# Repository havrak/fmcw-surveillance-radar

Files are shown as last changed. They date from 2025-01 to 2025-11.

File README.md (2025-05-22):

# FMCW Surveillance Radar

This is repo for my bachelors thesis.
This thesis presents the development of a surveillance radar system utilizing the SiRad Easy FMCW module.
FMCW (Frequency-Modulated Continuous Wave) technology enables precise distance measurement of targets while maintaining low power consumption.
Initially, the module’s capabilities are analyzed to identify its operational limits.
A custom two-axis rotary platform is then designed and constructed to enable mechanical beam steering, achieving three-dimensional spatial scanning.
The platform is controlled by an ESP32C6 microcontroller, implementing a G-code-like command interface for convenient operation.
MATLAB is employed to integrate the radar module with the platform to process the acquired data.
While the system’s performance limitations preclude real-time tracking of moving targets, it demonstrates functionality in monitoring diverse static environments, ranging from high-resolution close-range applications to long-range detection of targets up to 300 meters.
To accommodate these use cases, the processing pipeline is designed for flexibility, enabled by great degree of configurability.

#### Two-Axis Platform

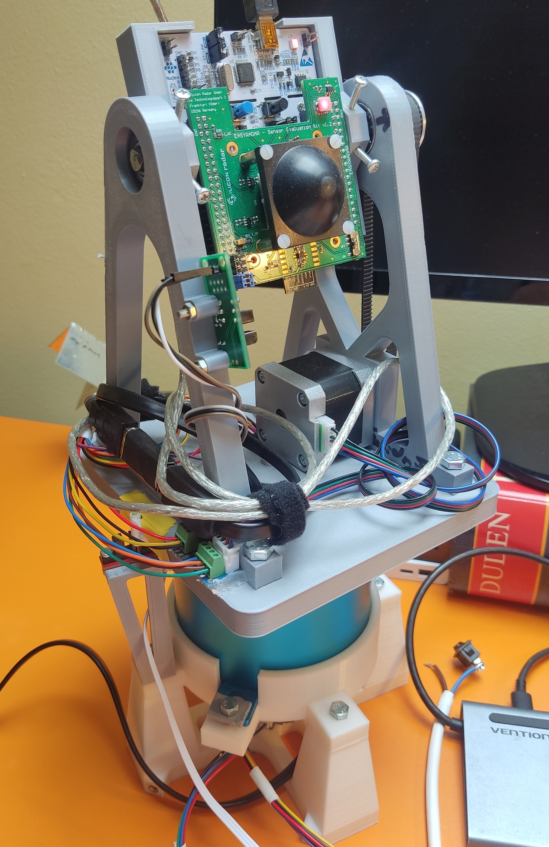
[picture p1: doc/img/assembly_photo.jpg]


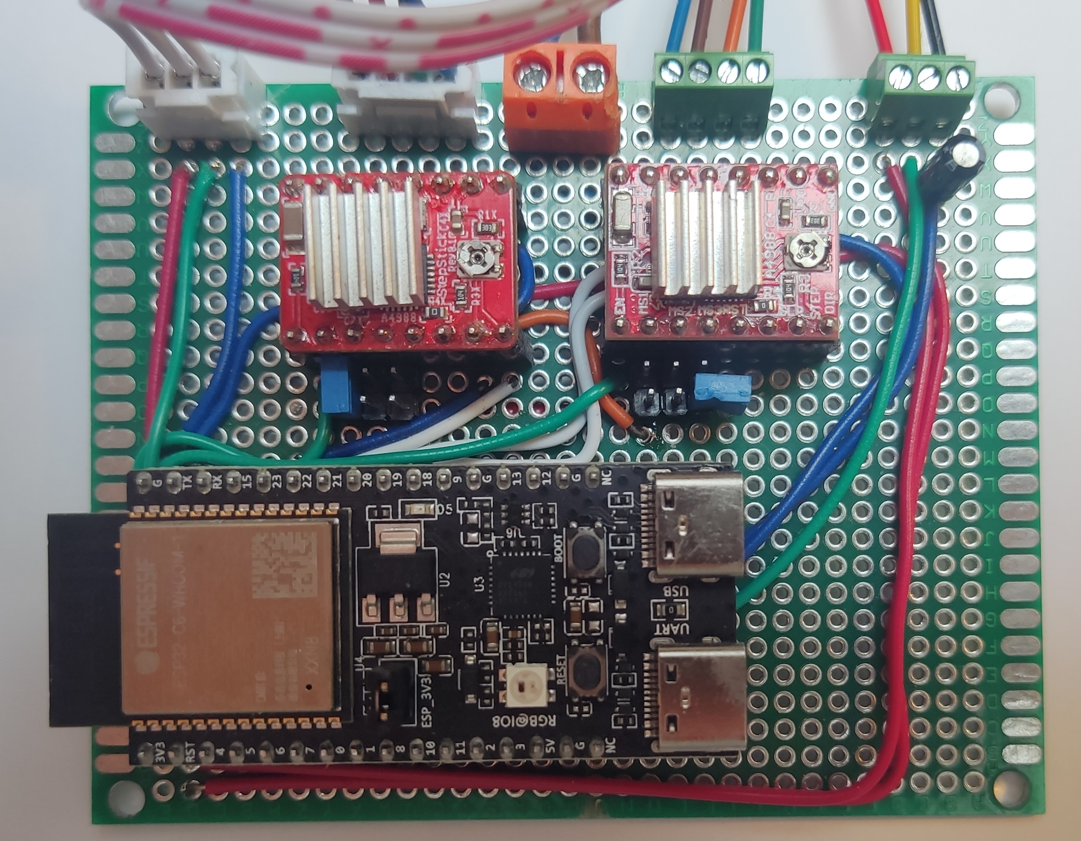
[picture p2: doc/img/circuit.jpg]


#### MATLAB application

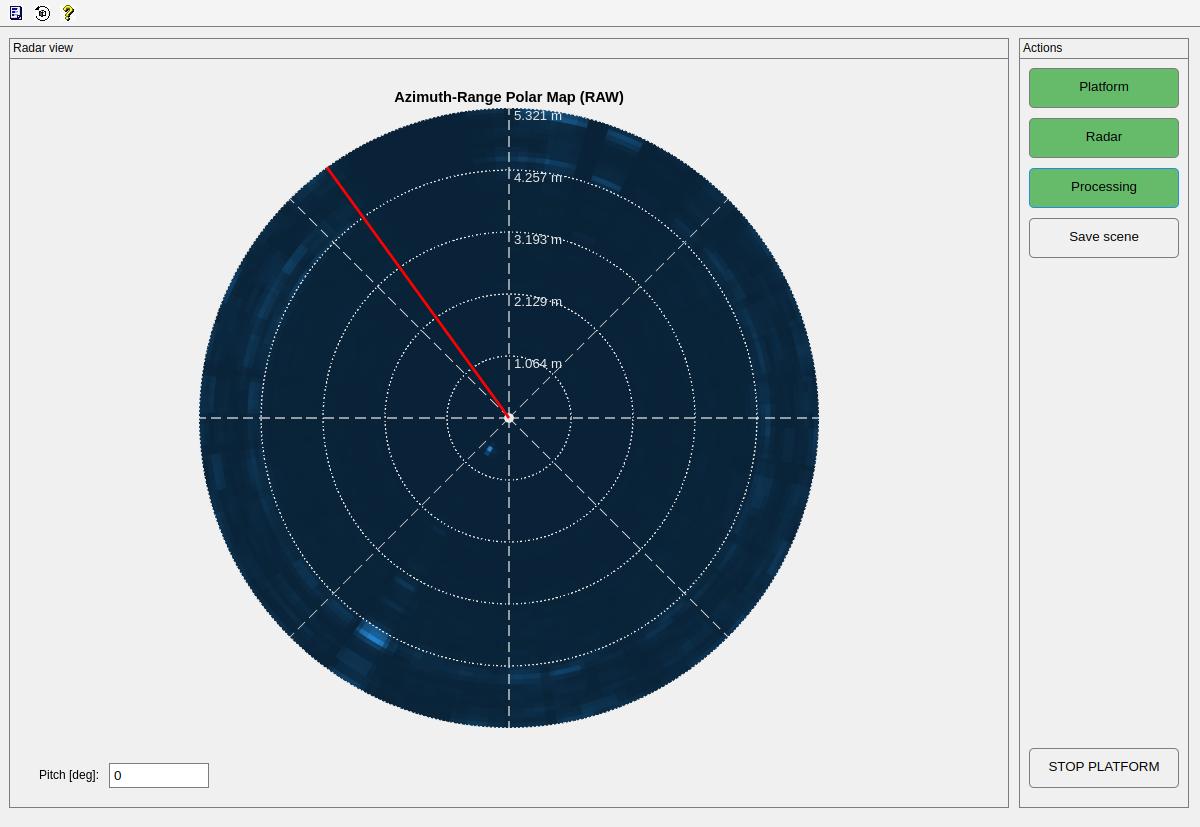
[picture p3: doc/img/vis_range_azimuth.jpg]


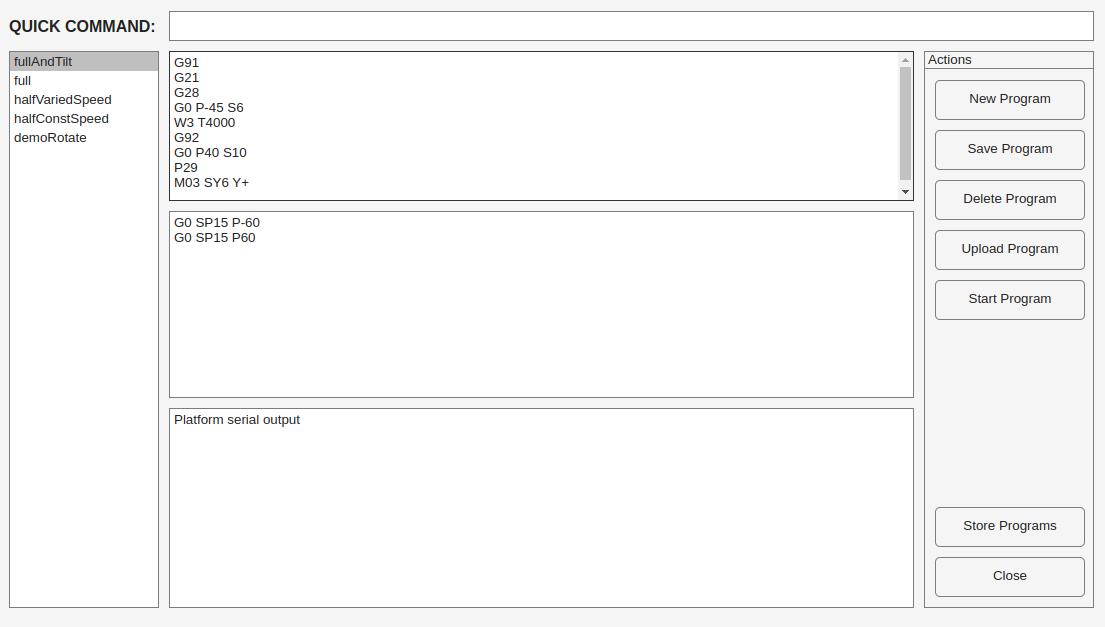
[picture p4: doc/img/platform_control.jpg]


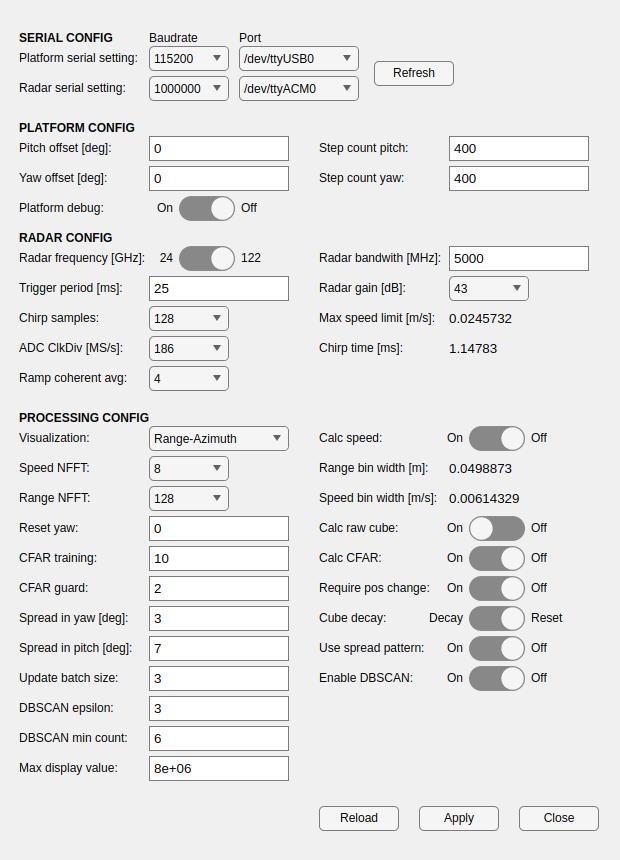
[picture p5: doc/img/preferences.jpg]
preferences


## Folder structure
* notes
	* personal notes on workings of Surveillance radars, ideas for processing and such
	* aren't part of any official publication of this thesis
* doc - full official documentation
* matlab - contains all MATLAB code that is responsible for processing data from the radar, displaying it and interfacing with indexing table
* indexing-table - contains all things related to custom two axis indexing table created for this project
	* esp32 - code for ESP32 microcontroller powering the indexing table
	* cad - cad files of mechanical parts and custom PCBs

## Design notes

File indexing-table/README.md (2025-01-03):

# Indexing table directory

This directory contains all resources regarding custom 2 axis rotary indexing table that has been constructed for this application.
Directory `esp32` concerns firmware for esp32 microcontroller driving the platform.
Cad directory than necessary cad files to 3D print additional components.

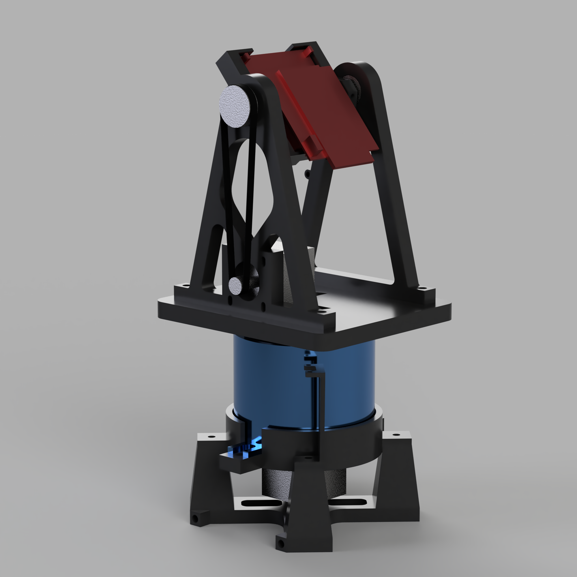
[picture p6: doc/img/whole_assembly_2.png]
render




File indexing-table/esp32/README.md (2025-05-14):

# ESP32 firmware to control indexing table
As of now code relies on proprietary libraries that are not included in this repository. After the project is closed to being finished, these libraries will be stripped to their bare minimum and included in this repository.

Following codebase is written entirely for esp-idf framework. While hal layer used is mimicking arduino, there are differences and thus simple porting of the code to arduino is not possible.
Configuration of the device is done primarily with Kconfig under esp-idf. While runtime configuration with storing to flash is possible, it is not needed for the current application and would result in unnecessary slowdowns.

# Constants
* these parameters are defined in Kconfig and will require recompilation of the firmware to change
* STEPPER_Y_STEP_COUNT, STEPPER_P_STEP_COUNT - number of steps in a single rotation on horizontal and pitch
	* can be changed on the fly with M92 command, however changes are not persistent
* STEPPER_Y_PIN_DIR, STEPPER_Y_PIN_STEP, STEPPER_P_PIN_DIR, STEPPER_P_PIN_STEP - pins used for direction and step signals
* STEPPER_Y_PIN_ENDSTOP, STEPPER_P_PIN_ENDSTOP - pins used for endstop signals
* STEPPER_MAX_SPEED - maximum speed in rpm
* STEPPER_DEFAULT_SPEED - default speed in rpm
* STEPPER_MIN_SPINDLE_TIME - minimum time in ms between two steps in spindle Mode
	* needed to maintain valid information about current position
	* never set bellow ~30 ms
* STEPPER_HAL_TIMER_PERIOD  - timer period (number of ticks per 1 period)
* STEPPER_HAL_TIMER_RESOLUTION - timer resolution (frequency of the timer)
	* these two influence how quickly will the 16 bit timer fill up, for higher RMP period must be lower, for lower RPM period must be higher

# Features
* two different units: degrees and steps
* two different positioning modes: absolute and relative
* common commands like simple movement, homing, setting speed and such, turning on/off are supported
* non standard GCode commands
	* imposing limits on movement - allowed positions of the steppers can be restricted
	* spindle mode - steppers can freely transitions between acting as steppers and as spindles (continuos motion)
	* programming - user can program in sequence of movements that can be executed with one command
		* these can be looped indefinitely or use simple one layer deep for loop
	* maintaining synchronization between two steppers
		* if both steppers are moving, next command is executed only after both steppers reach their target

## Behavior of limits
* user can impose limits on movement of both steppers this can be done via M201 command
* if user wishes to disable limits, they can do so with M202 Command
* movement must be restricted from two sides, restricting only one side doesn't make any sense as we are spinning in a circle
* limits are within single rotation of stepper, it is impossible to allow limited number of full rotations
* there are two possible basic setting for angles
	* low < high - we are restricted to range [low, high]
	* low > high - we are restricted to range [low, 360] U [0, high]

### Absolute positioning
* all angles are automatically normalized to [0, 360] range, or [0, STEP_COUNT] if we are in steps mode
* no limits
	* stepper will take shortest path to the target
* range: [low, high]
	* if target is outside of the range, it will be adjusted to the closest limit
	* than movement is rather straightforward as we can move only in one direction
* range: [low, 360] U [0, high]
	* if target is outside of the range, it will be adjusted to the closest limit
	* we firstly calculate average of the two limits than:
		* anything in [0, avg] is adjusted to high
		* anything in [avg, 360] is adjusted to low
	* again only one direction of movement is possible

### Relative postioning
* number of steps in single command is limited to +-32767, this is hardware/esp-idf private API limitation and cannot be changed
* no limits
	* stepper will do as many steps as are requested (limited to +-32767)
* range: [low, high]
	* if target is outside of the range, it will be adjusted to the closest limit
* range: [low, 360] U [0, high]
	* if target is outside of the range, it will be adjusted to the closest limit
	* if we are decrementing the angle we can only go to high limit
	* if we are incrementing the angle we can only go to low limit

# Communication

WARNING: DO NOT use this device without first reading the documentation. Commands might have similar names and structures as in common G-code but their behavior can be radically different as this device has rather specific requirements.

## Motor control
* axis descriptors: Y for yaw (horizontal) and P for pitch (tilt)
* M80: turn on high voltage power supply
* M81: turn off high voltage power supply
* M82: stop steppers and clear queues
* G20: set units to degrees
* G21: set units to steps
* G90: absolute positioning
	* Y - set absolute positioning on yaw
	* P - set absolute positioning on pitch
	* NOTE: absolute positioning is not available in spindle mode, if you issue a M03 command to stepper in absolute positioning mode, it will be automatically switched to relative positioning and throw an error
	* if no argument is provided both axis are switched to relative positioning
* G91: sets relative positioning
	* Y - set relative positioning on yaw
	* P - set relative positioning on pitch
	* if no argument is provided both axis are switched to relative positioning
* G92: set current position as 0
	* Y - set current position as 0 on yaw
	* P - set current position as 0 on pitch
	* if no argument is provided both axis are set to 0
	* NOTE: executes only when no other commands are queued in stepper queues
* G28: auto home
	* Y - home yaw
	* P - home pitch
	* if no argument is provided both axis are are homed
* stepper mode
	* only active if spindle mode is off
	* G0: move to/by given angle/steps
		* S<SPEED> - fallback speed
		* SY<SPEED> - speed for yaw motor
		* Y - angle by/to rotate in yaw
		* SP<SPEED> - speed for pitch motor
		* P - angle by/to rotate in pitch
		* speed needs to be provided, if number of steps is set but speed is not ERR 2 is returned
* spindle mode
	* beware when using spindle in programming mode one can desynchronized two command queues, this "issue" will be fixed and is up to user to handle as there is no clear way to decipher user intentions in programm in order to prevent it
	* M03:  Start spindle mode
		* S<SPEED> - fallback speed
		* SY<SPEED> - speed for yaw motor
		* Y<+/-> - start spin with yaw motor clockwise/anticlockwise
		* SP<SPEED> - speed for pitch motor
		* P<+/-> - start spin pitch motor clockwise/anticlockwise
		* NOTE: spindle will always spin at least for STEPPER_MIN_SPINDLE_TIME ms, thus theoretically to spin for N seconds would would have to substract STEPPER_MIN_SPINDLE_TIME from the time you want to spin, however timing here is quite finicky so correction probably will not secure exact number of steps
	* M05:  Stop spindle spinning.
		* Y - stop spindle regime on yaw
		* P - stop spindle regime on pitch
		* NOTE: spindle mode will also automatically end if stepper receives G0 command or if another M03 command is issued
		* if no argument is present neither axis will be stopped
* M92: set step count on steppers
	* Y<STEPS: set step count on Yaw
	* P<STEPS>: set step count on Pitch
	* default step count is defined in Kconfig
* M201: set limits on steppers
	* LY<ANGLE>: low limit on yaw
	* HY<ANGLE>: high limit on horizontal Stepper
	* LP<ANGLE>: low limit on pitch
	* HP<ANGLE>: high limit on pitch
	* ANGLE is given in degrees if unit is set to degrees (0-360), otherwise in steps (0-STEP_COUNT)
	* either no limits are placed on axis or both limits are placed, if user tries to impose just one limit whole axis will not be processed
	* NOTE: keep in mind that if limits are imposed and current postion is not within them, you will have to get the device within limits in one G0 command
* M202: disable limits
	* Y - disable limits on yaw
	* L - disable limits on pitch

### Programming movements
* device allows to preprogram sequence of movements that can be executed with one command, or looped continuously
* programms are not stored in flash, but in ram for now. Permanent storage of movements is done in MATLAB's programm configuration file
* if programm requires movement on both axis it is executed in parallel and next command is executed only after both axis reach their target
* program structures
	* header declaration
		* executed only once
		* used to set initial position, units, positioning mode, or home the device
	* main body
		* used for actual movement
		* if command P29 is issued it will be executed in a loop indefinitely loop
		* can be left empty
* P0 - stop executing programm (only one programm can be active at one time)
* P1 <command_id> - run command with given id
* P2 <command_id - delete command with given id
* P90 <command_id> - start programming mode with given id
	* if programm already exists it will be overwritten, changing programs post creation is not possible
	* upon entering programming mode all commands are stashed and not executed
	* programming begins with header declaration
		* commands declared in header are executed before any other commands
		* if programm is looped, header will be executed only once
		* can be used to set initial position, units, positioning mode, or home the device
* P91: called within programming context, advances programming from header declaration to main body
* P92: ends programming of the main body
	* NOTE: if loops are not closed, programm will not be saved and P92 command is disregarded
* P21: for loop declaration
	* I<ITERATIONS> - number of iterations for loop will take
* P22: end of loop
	* if iterations are not exhausted, programm will jump back to P21 (respectively command right after it)
* P29: declares looped programm, these programs will loop indefinitely until stopped
	* NOTE: only applicable in header declaration
* W0: wait command (seconds)
	* Y<TIME> - wait on yaw
	* P<TIME> - wait on pitch
* W1: wait command (milliseconds)
	* Y<TIME> - wait on yaw
	* P<TIME> - wait on pitch

#### Example of programming

| Command | Mode | Description |
|---|---|---|
| P90 prog | General -> Header dec  | start programming mode with programm id of 1 |
| G91 | Header dec | set relative positioning |
| G20 | Header dec | set units to degrees |
| G92 | Header dec | set current position as home |
| P29 | Header dec | declare looped programm |
| M03 SY6 Y+ | Header dec -> Main dec | set yaw to be in spindle mode |
| P91 | Main dec | start declaration of main loop |
| G0 SP30 P100  | Main dec | move pitch by 100 degrees at 30 rpm |
| G0 SP30 P-100 | Main dec | move pitch by -100 degrees at 30 rpm |
| P92 | Main dec | end programming |

### Special advanced commands
* WARN: usage of these commands is not recommended and can lead to unexpected behavior
* their primary usecase is to enable real time control over the device - for example to do tracking of some object
* M82: stop steppers and clear queues
	* similar to M80, however stop command is issued to the steppers instead of shutting them down
	* this means steppers will finish their current movement and then stop - thus data about current position should be still valid
	* used in conjunction with G3 to setup environment for real time control
* G3: direct control over steppers
	* G3 command skip whole scheduling routine and put command directly into stepper queues
	* NOTE: limits are not and cannot be checked
	* NOTE: all values are interpreted as steps
	* NOTE: if M82 is issued beforehand than G3 command should not lead to invalidation of current position
	* S<SPEED> - fallback speed
	* SY<SPEED> - speed for yaw
	* Y - angle by/to rotate in yaw
	* SP<SPEED> - speed for pitch
	* P - angle by/to rotate in pitch
* W3: wait in application layer
	* T<TIME> - time to wait for in ms
	* pauses execution in application layer

# Uplink from the device
* !P <TIMESTAMP>, <HORIZONTAL_ANGLE>, <TILT_ANGLE>
	* roughly every 20 ms device sends its current postion up with serial line
* !R OK or !R ERR <CODE>
	* upon receiving command from the host, device will send back an acknowledgement
	* in case of an error reported please consult following table

| Error code | Description |
|---|---|
| 1 | command wasn't able to be decoded |
| 2 | command code is valid but it's arguments aren't |
| 3 | command was processed, should be added to noProgrammQueue but we failed to get a lock |
| 4 | command exists but isn't yet supported by the hardware |
| 5 | we are either running homing or some programm thus new incoming commands will not be process |
| 6 | command might be fine but code runned into unexpected occurrence |
| 7 | indicated that program has unclosed for loop, it is recommended to delete whole program and start again |
| 8 | command is not valid in current context |

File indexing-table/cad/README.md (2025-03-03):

# CAD files for the indexing table

This directory contains CAD files for the indexing table. Models are exported as Fusion Archives.

* **static base v2** - main base on which entire structure rests
* **slipring mounting bracket** - mounting bracket that fixes slipring to static base
* **horizontal endstop holder** - attaches to slipring mounting bracket and provides mounting points for horizontal endstop
* **rotary base 1** - mount on top of slipring and provides points to attach rest of superstructure
* **SiDAR mount** - bracket to hold SiDAR devkit and enable tilt
* **superstructure left** - attaches to rotary base, holds radar and provides mounting point for tilt endstop
* **superstructure right** - attaches to rotary base, holds radar and tilt stepper motor

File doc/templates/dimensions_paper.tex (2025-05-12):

%%% Different page dimensions used on thesis
\def\PageLayoutSingle{single}
\def\PageLayoutSingleNoPrint{single-no-print}
\def\PageLayoutDouble{double}
\def\PageLayoutDoubleNoPrint{double-no-print}

%% Single page print
\ifx\PageLayout\PageLayoutSingle
\documentclass[a4paper,oneside,12pt]{report}
\setlength\textwidth{145mm}
\setlength\textheight{251mm}
\setlength\oddsidemargin{15mm}
\setlength\evensidemargin{15mm}
\setlength\topmargin{-0.4in}
\setlength\headsep{10mm}
\setlength\headheight{0mm}
\let\openright=\clearpage
\fi

%% Double page print
\ifx\PageLayout\PageLayoutDouble
% \documentclass[12pt,a4paper,twoside,openright]{report} % chapter will always start on the right side
\documentclass[12pt,a4paper,twoside]{report}
\setlength\textwidth{145mm}
\setlength\textheight{251mm}
\setlength\oddsidemargin{14.2mm}
\setlength\evensidemargin{0mm}
\setlength\topmargin{-0.4in}
\setlength\headsep{10mm}
\setlength\headheight{0mm}
\let\openright=\clearpage
% \let\openright=\cleardoublepage
\fi

%% Double page without space left for binding
\ifx\PageLayout\PageLayoutDoubleNoPrint
% \documentclass[12pt,a4paper,twoside,openright]{report} % chapter will always start on the right side
\documentclass[12pt,a4paper,twoside]{report}
\setlength\textwidth{145mm}
\setlength\textheight{251mm}
\setlength\oddsidemargin{9mm}
\setlength\evensidemargin{9mm}
\setlength\topmargin{-0.4in}
\setlength\headsep{10mm}
\setlength\headheight{0mm}
\let\openright=\clearpage
% \let\openright=\cleardoublepage
\fi

%% Single page without space left for binding
\ifx\PageLayout\PageLayoutSingleNoPrint
\documentclass[12pt,a4paper]{report}
\setlength\textwidth{145mm}
\setlength\textheight{251mm}
\setlength\oddsidemargin{9mm}
\setlength\evensidemargin{9mm}
\setlength\topmargin{-0.4in}
\setlength\headsep{10mm}
\setlength\headheight{0mm}
\let\openright=\clearpage

\fi

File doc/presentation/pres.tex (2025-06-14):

\documentclass[aspectratio=169]{beamer}
	\usepackage{tikz}
	\usepackage{tikz-cd}

	\usetikzlibrary{calc}
	\usetikzlibrary{fadings}
	\usetikzlibrary{shapes.geometric, arrows, positioning}

	\tikzstyle{layerheader} = [rectangle, minimum width=3cm, minimum height=1cm, text centered, draw=black, fill=gray!30]
	\tikzstyle{startstop} = [ellipse, minimum width=3cm, minimum height=1cm, text centered, draw=black, fill=red!30]
	\tikzstyle{process} = [rectangle, minimum width=3cm, minimum height=1cm, text centered, draw=black, fill=blue!20]
	\tikzstyle{decision} = [diamond, minimum width=2.5cm, minimum height=1cm, text centered, draw=black, fill=green!20]
	\tikzstyle{arrow} = [thick,->,>=stealth]

\usetheme{Berlin}
\usepackage[czech]{babel}
\usecolortheme{dolphin}
\usepackage{graphicx}
\usepackage{dirtree}
\usepackage{listings}
\usepackage[T1]{fontenc}
\usepackage{lmodern}
\usepackage[utf8]{inputenc}
\usepackage{caption}
\usepackage{bbding}
\usepackage{xurl}
\usepackage{scrextend}
\usepackage{appendixnumberbeamer}

\captionsetup{labelformat=empty}

\beamertemplatenavigationsymbolsempty
% \defbeamertemplate*{title page}{customized}[1][]
% {
% 	\usebeamerfont{title}\inserttitle\par
% 	% \usebeamerfont{subtitle}\usebeamercolor[fg]{subtitle}\insertsubtitle\par
% 	\bigskip
% 	\usebeamerfont{author}\insertauthor\par
% 	\usebeamerfont{institute}\insertinstitute\par
% 	\usebeamerfont{date}\insertdate\par
% 	\usebeamercolor[fg]{titlegraphic}\inserttitlegraphic
% }

\hypersetup{unicode}
\hypersetup{breaklinks=true}

\title{FMCW Surveillance Radar}
% \subtitle{----}
\author{Havránek Kryštof}
\date{June 2025}
\institute{České vysoké učení technické v Praze}
\setbeamertemplate{sidebar right}{}
\setbeamertemplate{footline}{%
\hfill\textbf{\insertframenumber{}/\inserttotalframenumber} \hspace{0.01cm} \vspace{0.1cm}}
\setbeamerfont{footnote}{size=\tiny}

\begin{document}

\begin{frame}[plain]
  \maketitle
\end{frame}

\clearpage
\setcounter{framenumber}{0}

\begin{frame}[fragile]
  \frametitle{Sections}

  \begin{enumerate}
    \item Surveillance FMCW Radar
    \item SiRad Easy
    \item Rotary Platform
    \item Desktop Application
    \item Conclusion
  \end{enumerate}
\end{frame}

\begin{frame}[fragile]
  \frametitle{Surveillance Radar}
  \section{FMCW Radar}

  \begin{itemize}
    \item Localization of target in plane or 3D space
    \item 2 basic approaches
      \begin{itemize}
        \item Electronic beamsteering: MIMO systems, complex processing, preferred for demanding applications
				\item Mechanically steered beam: simpler, easier processing, cheaper, less reliable
      \end{itemize}
    \item Generally based on pulsed radars
  \end{itemize}
\end{frame}

\begin{frame}[fragile]
  \frametitle{FMCW Radar}
  \begin{figure}[!htb]
    \begin{minipage}{0.48\textwidth}
      \begin{itemize}
        \item Broadcasts frequency modulated signal
        \item Low power consumption with great ranger resolution
        \item Range of target: proportional to beat frequency
        \item Speed of target: causes phase shift across many chirps
      \end{itemize}
    \end{minipage}\hfill
    \begin{minipage}{0.48\textwidth}
      \centering
      \begin{tikzpicture}[>=latex, scale=0.6]

        % Axes
        \draw[->] (0, 0) -- (8, 0) node[below] {$t$};
        \draw[->] (0, 0) -- (0, 5) node[left] {$f$};

        % Horizontal lines for BW
        \draw[dashed] (0, 4.5) -- (7.5, 4.5);
        \draw[dashed] (0, 1) -- (7.5, 1);
        \draw[dashed] (2.5, -0.05) -- (2.5, 4.7);

        % Labels for fc and BW
        \node[left] at (0, 0.7) {$f_c$};
        \draw[<->] (-0.5, 1) -- (-0.5, 4.5) node[midway,left] {$BW$};

        % Triangular wave for Tx
        \draw[thick,blue] (0, 1) -- (2.5, 4.5);
        \draw[thick,blue]	(2.5, 1) -- (5, 4.5);
        \draw[thick, dashed, blue] (5, 1) -- (6, 2.4);

        % Triangular wave for Rx (offset version)
        \draw[thick,red] (0.5, 1) -- (3, 4.5);
        \draw[thick,red] (3, 1) -- (5.5, 4.5);
        \draw[thick, dashed, red] (5.4, 1) -- (6.4, 2.4);

        % Label for Tch
        \draw[-] (2.5, -0.05) -- (2.5, 0.05) node[below] {$T_{\text{ch}}$};

        % Labels for Tx and Rx
        \node[blue] at (4.2, 4.1) {\small Tx};
        \node[red] at (5.3, 3.7) {\small Rx};

        % Sweep slope and fb
        \draw[<->] (1, 1) arc[start angle=0, end angle=55, radius=1];
        \node at (1.5, 1.3) {\small $k_{\text{sw}}$};
        \draw[<->] (1.5, 2.37) -- (1.5, 3.12) node[above, left] {$f_b$};

        % Small time delay (tau)
        \draw[<->] (2.5, 0.7) -- (3, 0.7) node[midway,below] {$\tau$};

      \end{tikzpicture}

      \caption{FMCW TX and RX Signal}
    \end{minipage}
  \end{figure}
\end{frame}

\begin{frame}[fragile]
  \frametitle{SiRad Easy}
  \section{SiRad Easy}
  \begin{figure}[!htb]
    \begin{minipage}{0.48\textwidth}
      \begin{itemize}
        \item Evaluation kit from Indie Semiconductors
        \item 24~GHz and 122~GHz transceivers modules
				\item Provides raw data from ADC converters over serial
        \item Slow update rate (at best around 20~ms)
          \begin{itemize}
            \item Max target speed bellow 1~ms/s
            \item Rotation speed limited to low RPM
          \end{itemize}
      \end{itemize}
    \end{minipage}\hfill
    \begin{minipage}{0.48\textwidth}
      \centering
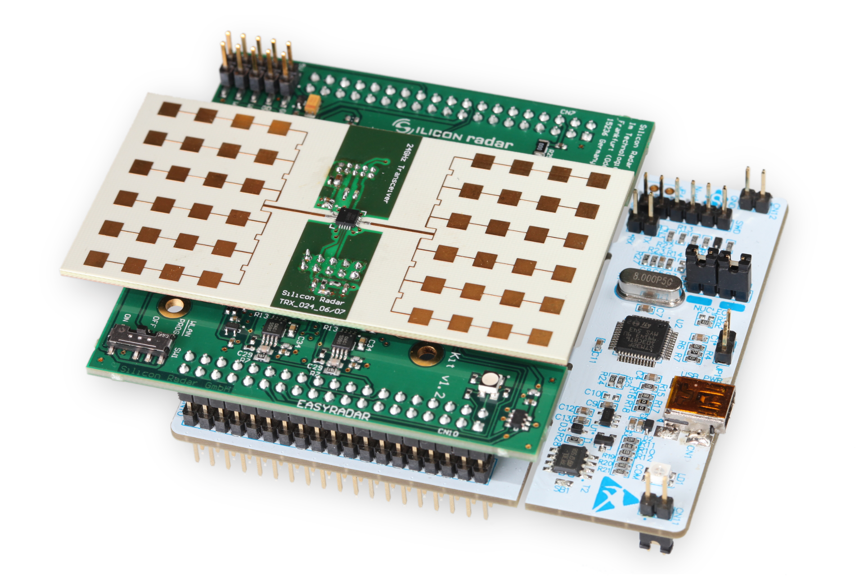
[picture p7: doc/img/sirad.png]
      

      \caption{SiRad Easy 24~GHz Configuration}
    \end{minipage}
  \end{figure}
\end{frame}

\begin{frame}[fragile]
  \frametitle{SiRad Easy: 24~GHz Module}
  \begin{figure}[!htb]
    \begin{minipage}{0.48\textwidth}
      \begin{itemize}
        \item Radiation characteristics simulated in CST studio
        \item 16 degrees in azimuth, 30 degrees in elevation
        \item Long range applications (300~m)
      \end{itemize}
    \end{minipage}\hfill
    \begin{minipage}{0.48\textwidth}
      \centering
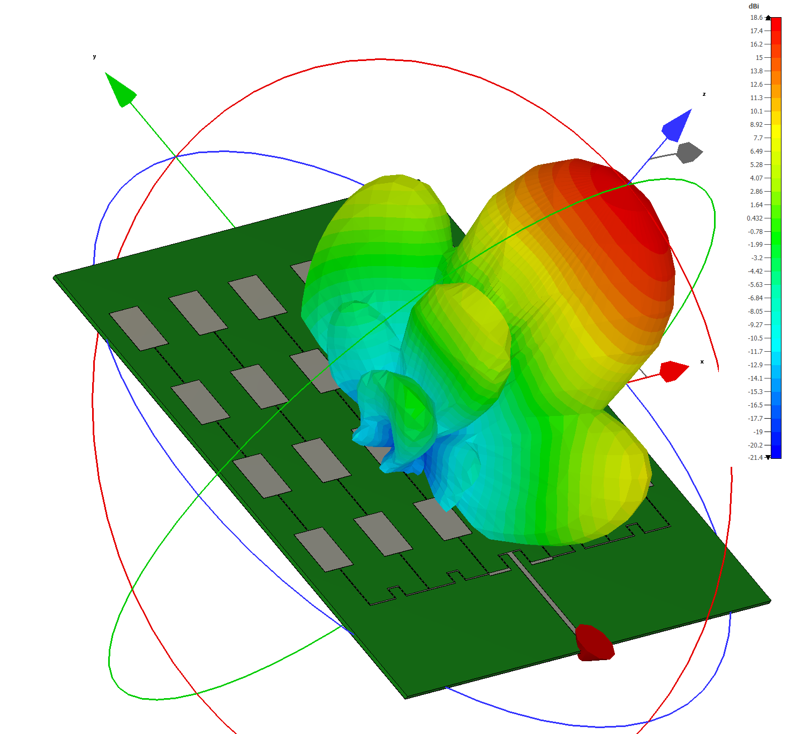
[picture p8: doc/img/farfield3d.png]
    
    \caption{Radiation Pattern of 24~GHz Header}
    \end{minipage}
  \end{figure}
\end{frame}

\begin{frame}[fragile]
  \frametitle{SiRad Easy: 122~GHz Module}
  \begin{figure}[!htb]
    \begin{minipage}{0.48\textwidth}
      \begin{itemize}
        \item Tight radar beam $\pm 4$° in both directions
        \item Measured maximal range of 30~m
        \item Ideal for close range, high resolution (5~cm) applications
      \end{itemize}
    \end{minipage}\hfill
    \begin{minipage}{0.48\textwidth}
      \centering
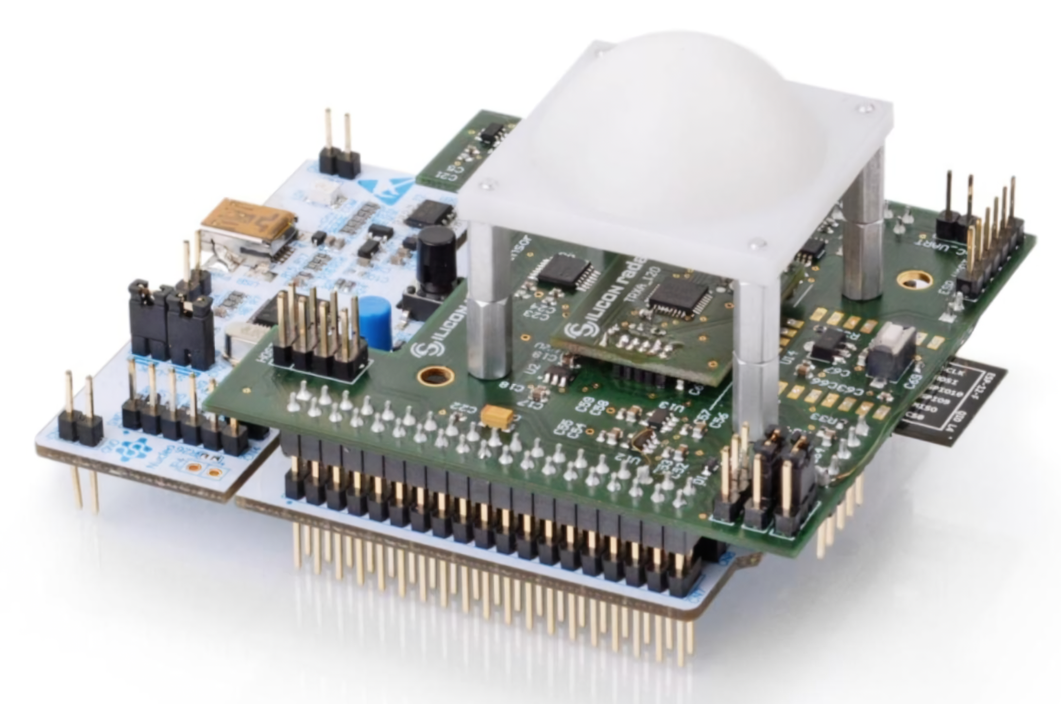
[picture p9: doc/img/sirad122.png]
      

      \caption{SiRad Easy 122~GHz Configuration }
    \end{minipage}
  \end{figure}
\end{frame}

\begin{frame}[fragile]
  \frametitle{Rotary Platform}
  \section{Rotary Platform}
  \begin{figure}[!htb]
    \begin{minipage}{0.48\textwidth}
      \begin{itemize}
        \item Two axis of movement, at low RPM
				\item Continuos rotation in azimuth
        \item ESP32C6 microcontroller
        \item G-Code-like API over serial
        \item Supports: automatic homing, relative/absolute positioning, spindle, preprogramming movement sequences
      \end{itemize}
    \end{minipage}\hfill
    \begin{minipage}{0.48\textwidth}
      \centering
      
      \caption{Platform with 122~GHz Module}
    \end{minipage}
  \end{figure}
\end{frame}

\begin{frame}[fragile]
  \frametitle{Platform Firmware Flow}

  \centering
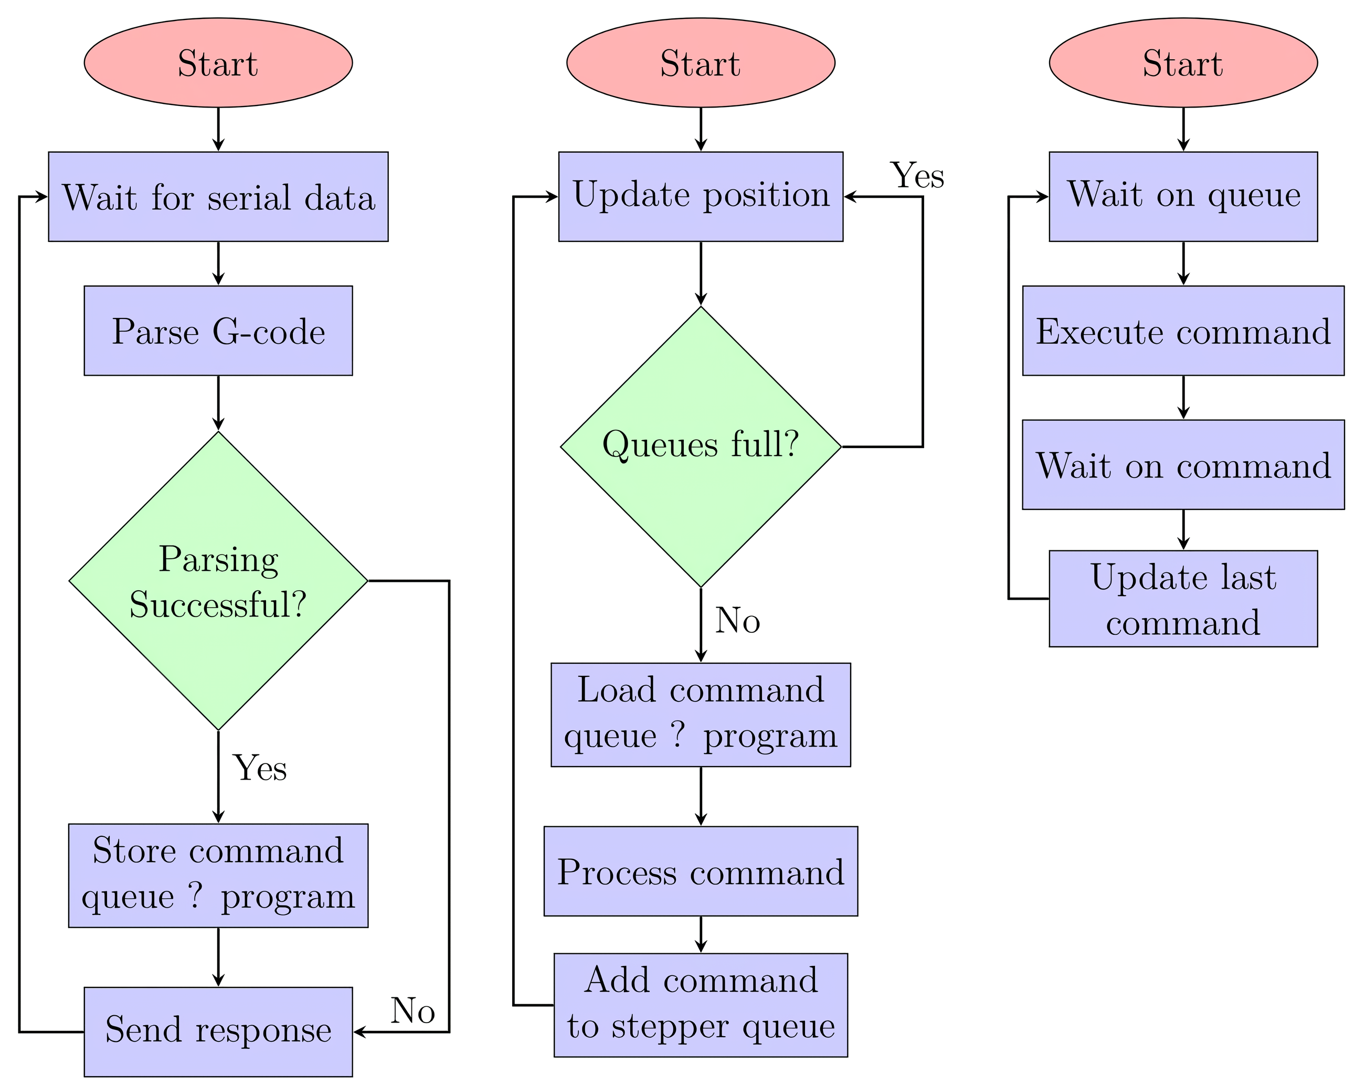
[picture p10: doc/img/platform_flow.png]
  

\end{frame}

\begin{frame}[fragile]
  \frametitle{Platform Program Example}
  \begin{tabular}{lll}
    \hline
    \texttt{Command}     & Mode   & Purpose                      \\
    \hline
    \texttt{P90 rotTilt} & Header & Initialize program rotTilt   \\
    \texttt{G91}         & Header & Set relative positioning     \\
    \texttt{G21}         & Header & Set units to steps           \\
    \texttt{G28}         & Header & Start auto home routine      \\
    \texttt{G0 P-50 S6}  & Header & Move pitch 50 steps          \\
    \texttt{W3 T5000}    & Header & Wait five second             \\
    \texttt{P92}         & Header & Set current position as home \\
    \texttt{P29}         & Header & Enable infinite looping      \\
    \texttt{M03 SY6 Y+}  & Header & Start Yaw spindle (6 RPM)    \\
    \texttt{P92}         & Header & Finalize header declaration  \\
    \texttt{G0 S5 P40}   & Body   & Pitch movement               \\
    \texttt{G0 S5 P-40}  & Body   & Return pitch                 \\
    \texttt{P92}         & Body   & Finalize program             \\
    \hline
  \end{tabular}
\end{frame}

\begin{frame}[fragile]
  \frametitle{Desktop Application}
  \section{Desktop Application}
  \begin{figure}[!htb]
    \begin{minipage}{0.48\textwidth}
  \begin{itemize}
    \item Control app written in MATLAB
    \item Integrates radar and platform data
    \item Offers wide degree of customization
  \end{itemize}
    \end{minipage}\hfill
    \begin{minipage}{0.48\textwidth}
      \centering
    
    \caption[]{Main App Window}
    \end{minipage}
  \end{figure}
\end{frame}

\begin{frame}[fragile]
  \frametitle{Preferences: Radar}
  \begin{center}
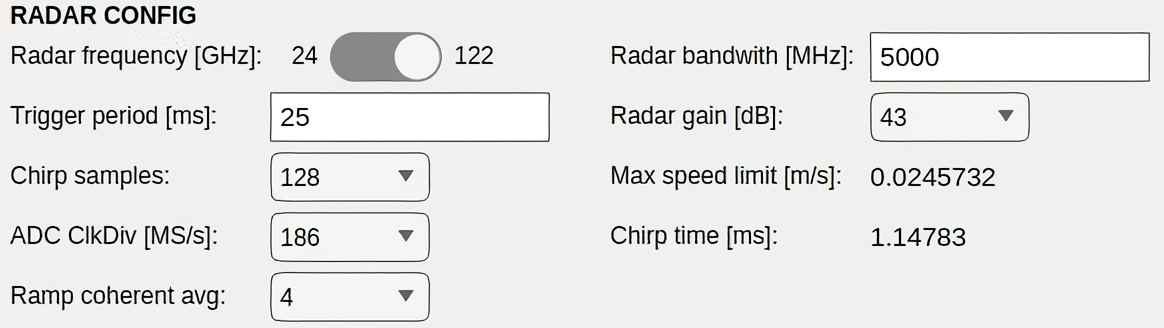
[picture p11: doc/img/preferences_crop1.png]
    
  \end{center}
\end{frame}

\begin{frame}[fragile]
  \frametitle{Preferences: Processing}
  \begin{center}
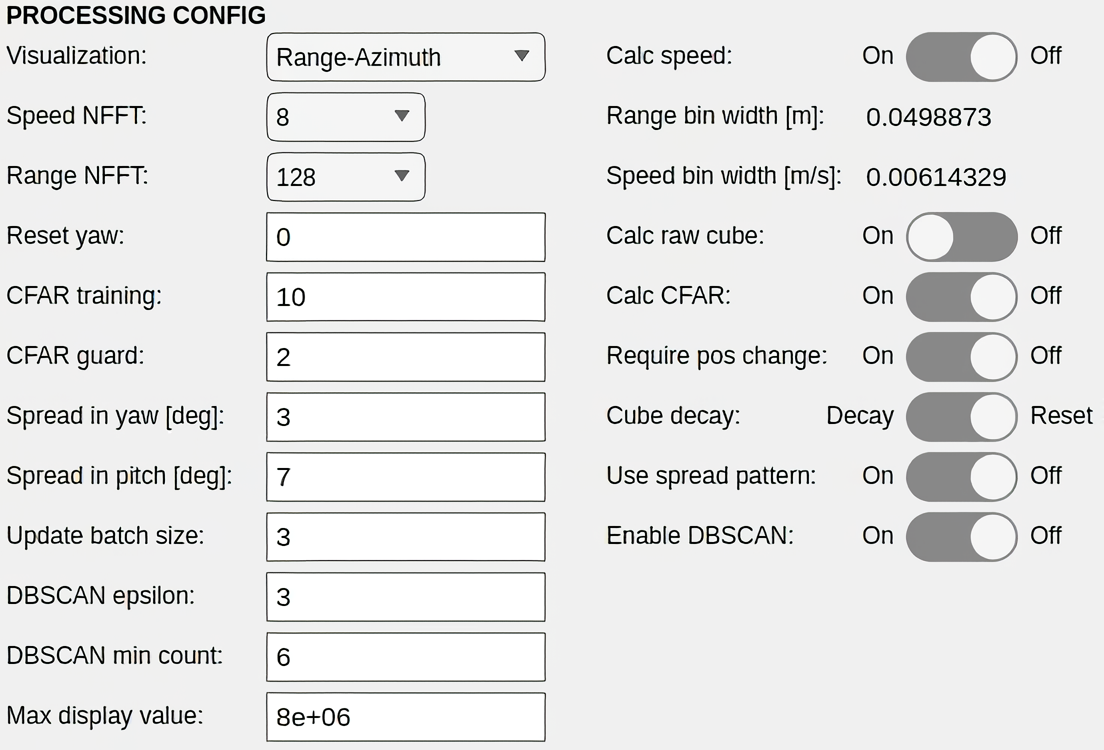
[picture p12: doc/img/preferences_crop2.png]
    
  \end{center}
\end{frame}

\begin{frame}[fragile]
  \frametitle{Data Aquisition}
  \begin{center}
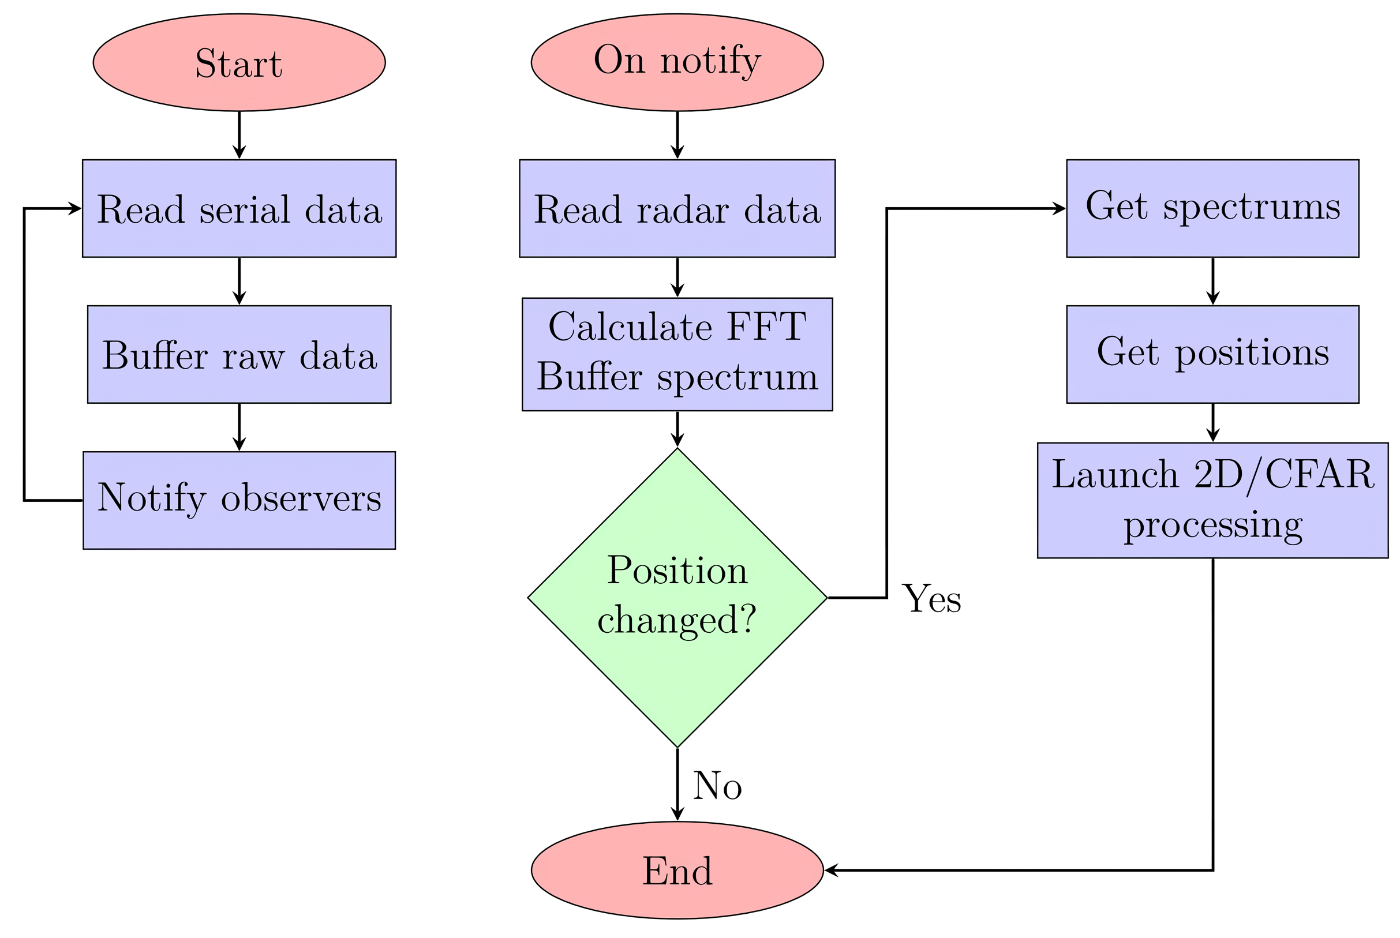
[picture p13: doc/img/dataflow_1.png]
    
  \end{center}
\end{frame}

\begin{frame}[fragile]
  \frametitle{Data Processing}
  \begin{center}
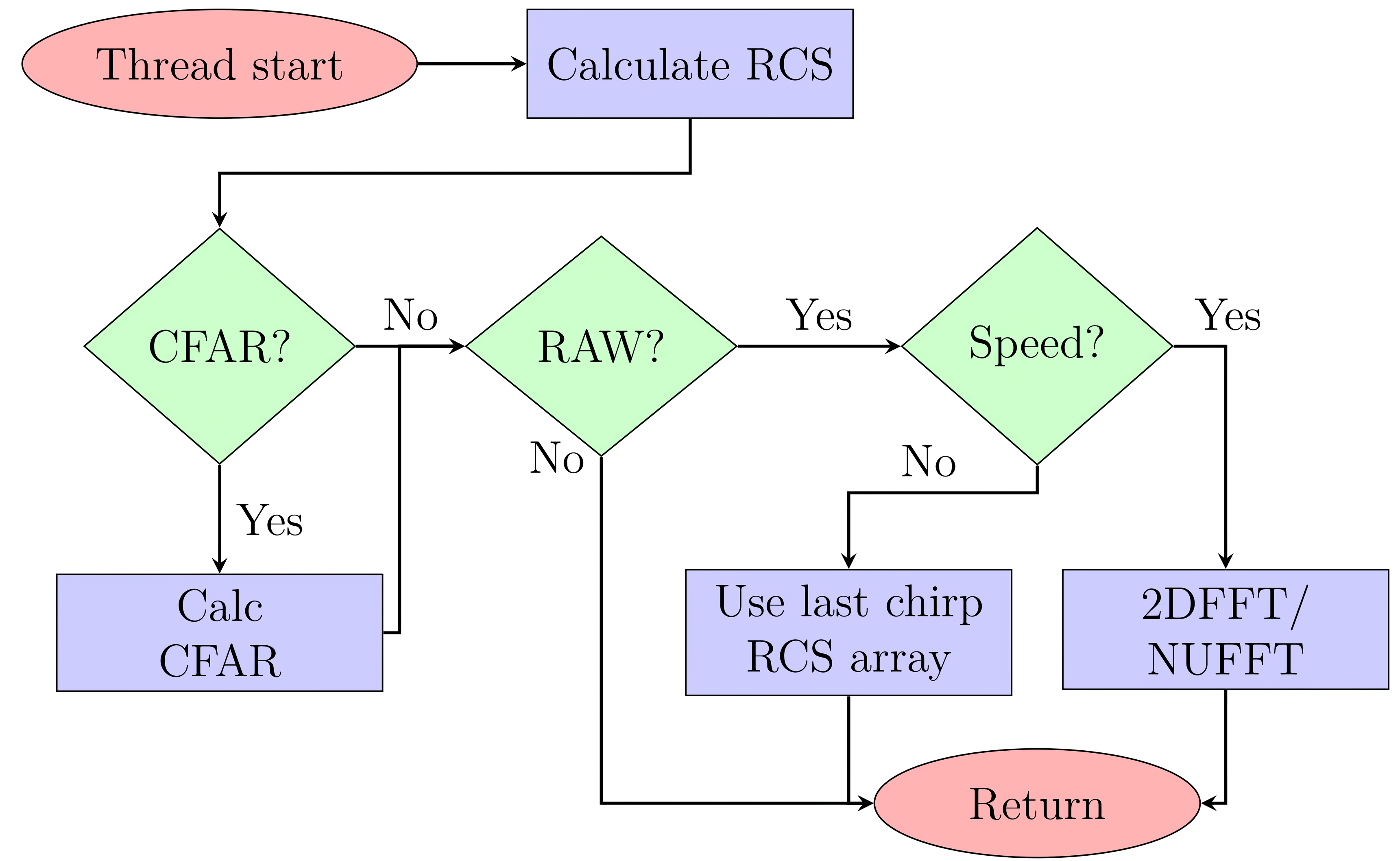
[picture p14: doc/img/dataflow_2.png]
    
  \end{center}
\end{frame}

\begin{frame}[fragile]
  \frametitle{Data Storing}
  \begin{center}
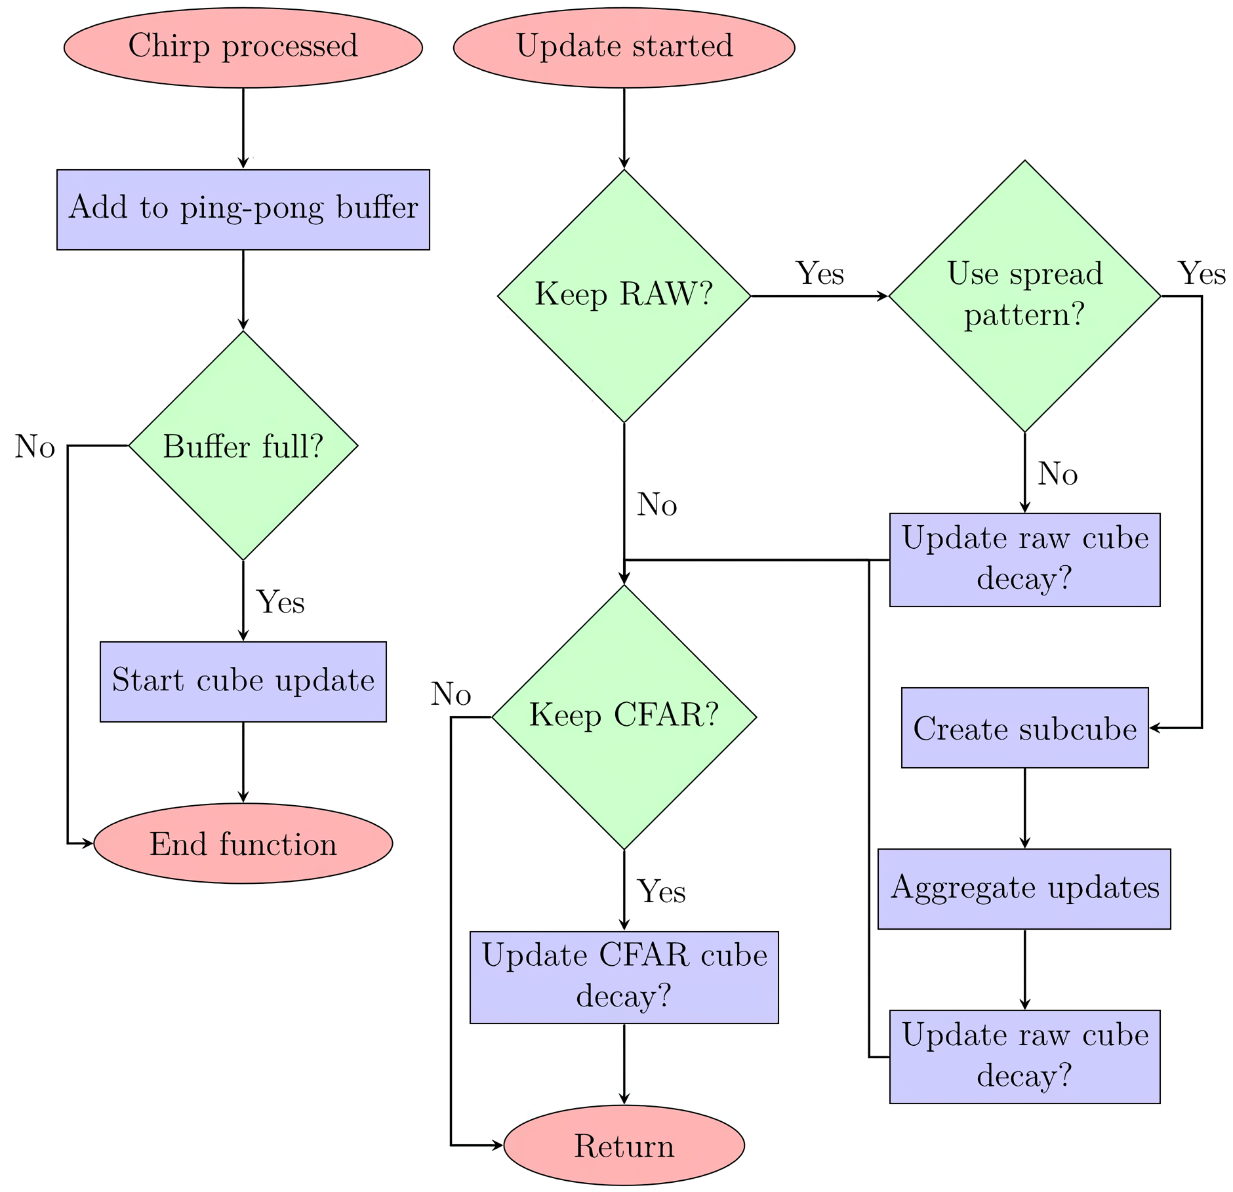
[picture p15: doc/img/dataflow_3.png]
    
  \end{center}
\end{frame}

\begin{frame}[fragile]
  \frametitle{Visualization}
  \begin{itemize}
    \item Data are only provided in a graphic way to the user
    \item Three visualization styles
      \begin{itemize}
				\item Range-RCS or Range-Doppler (fixed azimuth and elevation)
				\item Range-Azimuth (fixed elevation)
        \item 3D
      \end{itemize}
  \end{itemize}
\end{frame}

\begin{frame}[fragile]
  \frametitle{Visualization: Range-RCS/Doppler}
  \begin{figure}[!htb]
    \begin{minipage}{0.48\textwidth}
      \centering
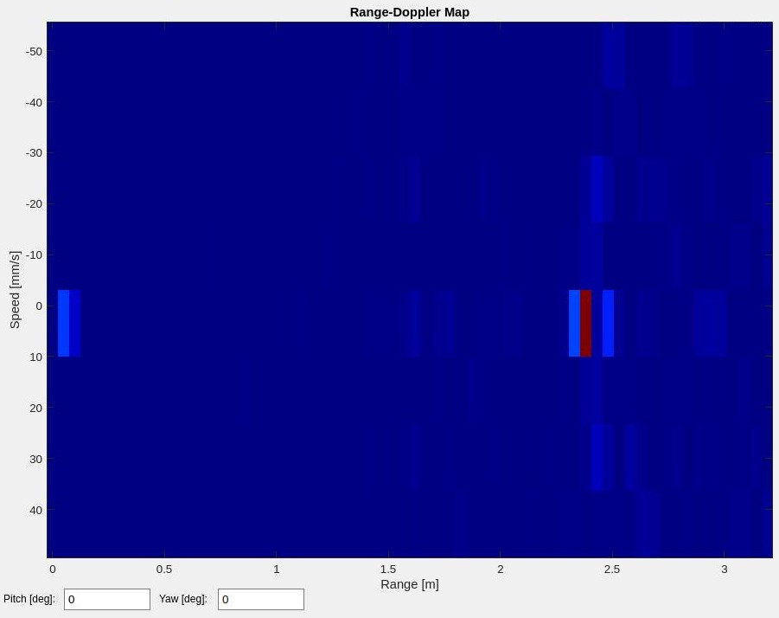
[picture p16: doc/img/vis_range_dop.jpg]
      
      \caption{Range-Doppler}
    \end{minipage}\hfill
    \begin{minipage}{0.48\textwidth}
      \centering
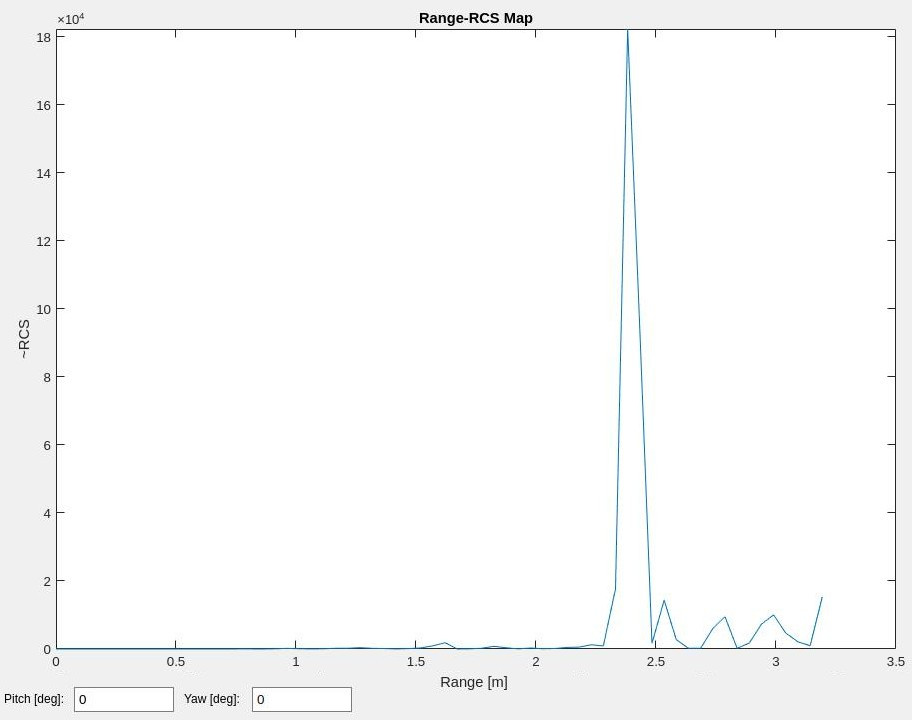
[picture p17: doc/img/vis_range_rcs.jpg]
      
      \caption{Ranger-RCS}
    \end{minipage}
  \end{figure}
\end{frame}

\begin{frame}[fragile]
  \frametitle{Visualization: Range-Azimuth}
  \begin{center}
    
  \end{center}
\end{frame}

\begin{frame}[fragile]
  \frametitle{Visualization: 3D}
  \begin{center}
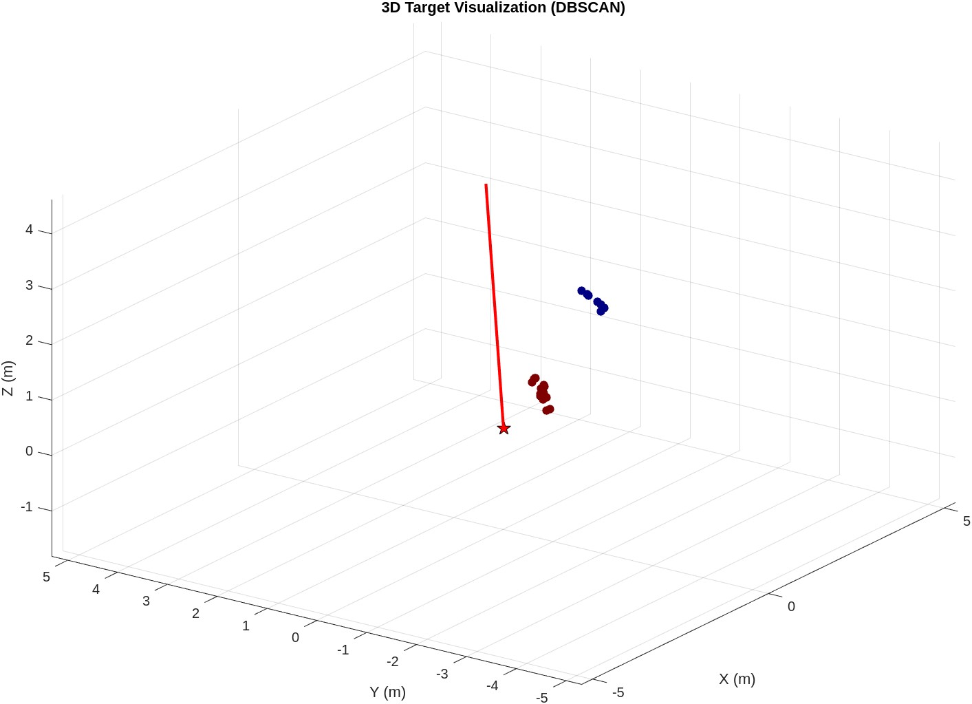
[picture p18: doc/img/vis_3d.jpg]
    
  \end{center}
\end{frame}

\begin{frame}[fragile]
  \frametitle{Conclusion}
  \section{Conclusion}
  \begin{itemize}
    \item SiRad Easy
      \begin{itemize}
				\item Sufficient for monitoring static scenes
        \item Speed estimation is limited -- tracking application isn't a possibility
      \end{itemize}
    \item Rotary platform
      \begin{itemize}
        \item Matches design requirements
        \item Underpowered azimuth motor and low belt tension
      \end{itemize}
    \item Desktop application
      \begin{itemize}
        \item Great degree of configuration
        \item Pipeline performant, except for final visualization under Linux
      \end{itemize}
  \end{itemize}
\end{frame}

\begin{frame}[fragile]
  \frametitle{Q1: Exprimental Data}

  \begin{itemize}
    \item Large number of parameters: header, bandwidth, gain, target, CFAR setting -- requires fine tuning
    \item Rotary movement + inconsistent radar timing complicate reproducibility
    \item Author couldn't establish correct, reproducible, validation methodology to give measured data any validity
    \item No testing in a controlled environment was done
    \item When static, the radar capabilities generally match advertised
      \begin{itemize}
        \item 122~GHz header -- Tight beam $\Rightarrow$ very sensitive to target orientation
      \end{itemize}
  \end{itemize}
\end{frame}

\end{document}

% Radarový modul je v práci pouze konfigurován v rámci výrobcem specifikovaných paramterů, veškerý další popisovaný kod je pak již moje práce

% Software běžící na mikrokontroléru je relativně přímočarý.
%

% Kvůli relativně obecnému zadání má aplikaci celou řadu nastavitelných paramterů
%
% Zpracování dat začíná vyčtením dat z radaru
%
%
% Po tomto krotku má program dva objekty - pole cílů z CFAR a range-Doppler mapu
%
%
% je li vyrovávací pamět plná, spustí se update radarové kostky v paralelním vlákně.
% Radar cube je základní datová struktura, která uchovává informace o prostoru v n dimenzionálnách polích.
%
% Takové kostky jsou v paměti dvě - jedna pro surová data, druhá pro CFAR výstup.
% Proces je paralelizován jelikož systém podporuje postupné stárnutí dat, což vyžaduje stovky tisíc floating point operací u větších kostek
%
%
% Shrnuto.
%
%

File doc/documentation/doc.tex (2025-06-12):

\def\PageLayout{single-no-print}
\def\DocLanguage{en}
\def\PackagesIncludeTikz{yes}
\def\PackagesIncludeBib{yes}

\input{metadata}
\input{../templates/dimensions_paper}
\input{../templates/packages}
\input{../templates/macros}
\input{../templates/xmp}
\input{../templates/doc_paper}

\addbibresource{bibliography.bib}
\usepackage{pdfpages}

\newcommand{\sirad}{SiRad Easy\textsuperscript{\copyright} }
\newcommand{\boldred}[1]{\textbf{\textcolor{red}{#1}}}
\newcommand{\boldblue}[1]{\textbf{\textcolor{blue}{#1}}}
% \newcommand{\red}[1]{\textcolor{red}{#1}}

\begin{document}

\include{title_page}

\tableofcontents

\newpage
\pagenumbering{arabic}
\setcounter{page}{1}

\include{abbreviations}

\include{introduction}

\pagestyle{fancy}

\chapter{FMCW Radar Fundamentals}

Classical CW (Continuous Wave) radars broadcast a signal only on a single frequency, while FMCW radars make a linear sweep across a given bandwidth.
This approach enables accurate range estimation at low power consumption and still allows speed measurements using the Doppler shift.
However, velocity calculations in FMCW radars are more complex compared to those in single-frequency CW radars.

The "MW" suffix in FMCW radar denotes that the system operates in the microwave frequency range.
These high frequencies enable the use of compact antenna arrays, which can sometimes even be integrated directly on-chip.
Additionally, the millimeter-wave portion of the spectrum is typically license-free \cite{spektrumCTU} and offers large bandwidths, reducing a risk of interference.

\section{Comparison FMCW Radar to Pulse Radar}

Distance measurement using radar predates FMCW technology by several decades.
Early radar systems primarily relied on pulsed signals, where distance can be calculated from the time of flight, $t$, of the signal as
\begin{equation}
  d = \frac{c_o \cdot t}{2}.
  \label{eq:distance}
\end{equation}
Speed calculation is also relatively straightforward, as the Doppler effect is quite clear
\begin{equation}
  v = \frac{f_\mathrm{dop} c_o}{2f_\mathrm{rad}},
  \label{eq:dopler}
\end{equation}
where $f_\mathrm{dop}$ is the Doppler frequency, $c_o$ is the speed of light and $f_\mathrm{rad}$ is the frequency of the radar signal \cite{jankiraman2018}.

While this approach is conceptually straightforward, it has several limitations, particularly in applications requiring high precision at close range.
Achieving fine resolution in distance measurement necessitates very short pulses.
However, to maintain sufficient SNR (signal-to-noise ratio), the transmitted pulse power per pulse must remain high, regardless of its width \cite{jankiraman2018}.

Maintaining high average transmission power poses legal and technical challenges.
Risk of interference with other devices is increased and such system demand bulky, high-power circuitry -- often with high voltages and even vacuum tubes.
Consequently, pulsed radar is predominantly used in applications where fine range resolution is not essential, such as long-range target detection.

One key advantage of pulsed radar is its relatively simple data processing.
In contrast, FMCW radar data processing is more complex due to the interdependence of distance and velocity measurements as both manifest themselves as frequency shift.

\section{Basic Principles of Ideal FMCW Radar}

Let us picture an ideal FMCW radar system placed in a scene with a single large target that reflects all incoming signals.
The radar is broadcasting with a periodically repeated frequency sweep from $f_\mathrm{c}$ to $f_\mathrm{c}+BW$ creating a sawtooth waveform.
Aside from a sawtooth, other modulations are also frequently used, such as linear triangular modulation or segmented linear frequency modulation.
These offer some advantages, but the nature of the beat signal, which forms a sine wave with sawtooth modulation, is more complex.
This is especially true in the case of triangle modulations when multiple targets are present \cite{jankiraman2018}.
\sirad kit, used in this thesis, technically uses a segmented linear frequency modulation due to its limited computational power \cite{siradPRO}, but its mathematical principles are similar to those for sawtooth.

\begin{figure}[h!]
  \centering
  \begin{tikzpicture}[>=latex, scale=1]

    % Axes
    \draw[->] (0, 0) -- (8, 0) node[below] {$t$};
    \draw[->] (0, 0) -- (0, 5) node[left] {$f$};

    % Horizontal lines for BW
    \draw[dashed] (0, 4.5) -- (7.5, 4.5);
    \draw[dashed] (0, 1) -- (7.5, 1);
    \draw[dashed] (2.5, -0.05) -- (2.5, 4.7);

    % Labels for fc and BW
    \node[left] at (0, 1) {$f_c$};
    \draw[<->] (-0.5, 1) -- (-0.5, 4.5) node[midway,left] {$BW$};

    % Triangular wave for Tx
    \draw[thick,blue] (0, 1) -- (2.5, 4.5);
    \draw[thick,blue]	(2.5, 1) -- (5, 4.5);
    \draw[thick, dashed, blue] (5, 1) -- (6, 2.4);

    % Triangular wave for Rx (offset version)
    \draw[thick,red] (0.5, 1) -- (3, 4.5);
    \draw[thick,red] (3, 1) -- (5.5, 4.5);
    \draw[thick, dashed, red] (5.4, 1) -- (6.4, 2.4);

    % Label for Tch
    \draw[-] (2.5, -0.05) -- (2.5, 0.05) node[below] {$T_{\text{ch}}$};

    % Labels for Tx and Rx
    \node[blue] at (4.2, 4.1) {\small Tx};
    \node[red] at (5.3, 3.7) {\small Rx};

    % Sweep slope and fb
    \draw[<->] (1, 1) arc[start angle=0, end angle=55, radius=1];
    \node at (1.5, 1.3) {\small $k_{\text{sw}}$};
    \draw[<->] (1.5, 2.37) -- (1.5, 3.12) node[above, left] {$f_b$};

    % Small time delay (tau)
    \draw[<->] (2.5, 0.7) -- (3, 0.7) node[midway,below] {$\tau$};

  \end{tikzpicture}

	\caption[Ideal relation of frequency on time for received and sent signal \cite{adler2023}]{Ideal relation of frequency on time for received and sent signal \cite{adler2023}}
  \label{fig:fmcw_ideal}
\end{figure}

We can clearly see that, in a given time $t$, the frequency spread from the sent signal to the received signal is proportional to the time delay $\tau$.
However, performing a simple subtraction in the spectrogram of both signals isn't really feasible; the calculation needs to take a smarter approach.

Let us define the chirp slope $k_\mathrm{sw}$ with which we can describe the change in frequency of the broadcasted signal as
\begin{equation}
  \Delta f_\mathrm{s}(t) = k_\mathrm{sw}t = \frac{BW}{T_\mathrm{ch}} t,
  \label{eq:deltaf}
\end{equation}
where $t$ is the time, ranging 0 to chirp length $T_\mathrm{ch}$.
The standard equation of an frequency modulated signal can be written as
\begin{equation}
  s_\mathrm{t}(t) = A \cos\left(\omega_c t + 2\pi \int_{0}^{t} f_\mathrm{s}(t) \mathrm{d}t\right),
  \label{eq:fm}
\end{equation}
where $A$ is the amplitude of the signal, $\omega_c$ is the carrier frequency and $f(s)$ is the frequency of the signal.
Substituting (\ref{eq:deltaf}) into (\ref{eq:fm}) we get the signal broadcasted by the radar \cite{suleymanov2016}
\begin{equation}
  s_\mathrm{t}(t) = A \cos(\omega_c t + \pi k_\mathrm{sw}t^2).
  \label{eq:fm2}
\end{equation}

The signal bounced back from a target will have the same equation, only shifted by the time delay $\tau$,
\begin{equation}
  s_\mathrm{r}(t) = A \cos(\omega_c (t - \tau) + \pi k_\mathrm{sw}(t - \tau)^2).
  \label{eq:fm3}
\end{equation}
Now we can calculate the product of the two signals; this can be done easily in the real world using a frequency mixer.
The result of the multiplication is  \cite{suleymanov2016}
\begin{align}
  s(t) = s_\mathrm{r}(t) \cdot  s_\mathrm{t}(t) & = \frac{A^2}{2}\cos\left(2(\omega_c - 2\pi k_\mathrm{sw}T_\tau)t + 2\pi k_{sw}t^2 + (\pi k_\mathrm{sw} \tau^2 - \omega_c \tau) \right)+ \nonumber \\
                                                & +\frac{A^2}{2} \cos\left(2\pi k_\mathrm{sw} \tau t + (\omega_c \tau - \pi k_\mathrm{sw} \tau^2)\right).
  \label{eq:fm4}
\end{align}
The first additive term will lead to a signal with a very high frequency, well above $2\omega_c$.
This term doesn't carry any useful information and is usually filtered out -- either by a low-pass filter or the frequency mixer itself.
The second term is the so-called beat signal, whose frequency is directly proportional to the time delay $\tau$.
Deriving the second argument by time, we get the frequency of the beat signal \cite{graham2005}
\begin{equation}
  f_\mathrm{b} = \frac{1}{2\pi}\frac{\partial}{\partial t} \left(2\pi k_\mathrm{sw} \tau t + (\omega_c \tau - \pi k_\mathrm{sw} \tau^2)\right) = k_\mathrm{sw} \tau.
  \label{eq:fb}
\end{equation}

Calculating the distance to a target is now trivial as the delay $\tau$ is equal to the time it takes for the signal to travel to a target and back \cite{graham2005}
\begin{equation}
  R = \frac{c_0 \tau}{2},
  \label{eq:distance2}
\end{equation}
By substituting (\ref{eq:fb}) into (\ref{eq:distance2}), we get the equation for a distance \cite{graham2005}
\begin{equation}
  R = \frac{c_0 f_\mathrm{b}}{2k_\mathrm{sw}}= \frac{c_o f_\mathrm{b} T_{\mathrm{ch}}}{2 BW}.
  \label{eq:distance3}
\end{equation}

\subsection{Limits of Range Measurement}

The maximal distance is given by the time it takes for the signal to travel from the radar to a target and back.
If the distance were greater than the time of a single chirp, the signal would be interpreted as coming from a closer target.
This gives us a maximal limit on the beat frequency, $f_\mathrm{b} = BW$.

However, in most cases, the limit will be imposed not by $T_\mathrm{ch}$ respectively $BW$ but by the sampling frequency $f_\mathrm{s}$.
In order to avoid aliasing, the Nyquist-Shannon theorem must be satisfied, thus limiting the maximal beat frequency to $f_\mathrm{s}/2$ and resulting in a maximal distance of \cite{jankiraman2018}
\begin{equation}
  R = \frac{c_o f_\mathrm{s}}{4k_\mathrm{sw}}.
  \label{eq:distance4max}
\end{equation}

While sampling with frequency $f_\mathrm{s}$ we get $N =\mathrm{f}_\mathrm{s} T_\mathrm{ch}$ samples.
Applying a DFT to the signal we get $N$ samples in spectrum with frequency resolution of
\begin{equation}
  \Delta f_\mathrm{b} = \frac{f_\mathrm{s}}{N} = \frac{1}{T_{ch}}.
  \label{eq:resolution}
\end{equation}
We can see that the resolution of the spectrum is only inversely proportional to the chirp length and doesn't have any relation to the sampling frequency  \cite{jankiraman2018}.
Now we can substitute $\Delta f_\mathrm{b}$ into (\ref{eq:distance3}) to get the minimal distance that can be measured as
\begin{equation}
  \Delta R = \frac{c_o}{2BW}
  \label{eq:distance5min}
\end{equation}
Thus, in order to increase resolution in range, a wider bandwidth is needed \cite{graham2005}.

There are, of course, other effects impeding the resolution of the radar system, such as phase noise around targets or sweep nonlinearity.
Sweep nonlinearity can be either in the ramp itself, leading to decreasing resolution with range (with both linear and quadratic errors present)  \cite{graham2005}, or in sweep recovery (time to return to the start of the sweep), which leads to a constant decrease in resolution \cite{piper1995}.
Both are, however, largely compensated in modern radar systems by using a closed feedback loop  \cite{graham2005}.

\subsection{Speed Measurement}

In order to demonstrate the effect of moving target on the beat frequency, we can redefine the time delay $\tau$ as
\begin{equation}
  \tau = \frac{2(R_0+vt)}{c_o}
  \label{eq:tau222}
\end{equation}
where $R_0$ is the initial distance to a target and $v$ is the radial speed of a target.
Within a single chirp, there is no way to distinguish between the effects of distance and speed of the target; thus, multiple chirps are needed \cite{suleymanov2016}.
We can rewrite the equation (\ref{eq:tau222}) as
\begin{equation}
  \tau = \frac{2(R_0 v(nT_\mathrm{ch} + t_\mathrm{s}))}{c_0}
  \label{eq:tau2}
\end{equation}
where $n$ is the number of chirps, $T_\mathrm{ch}$ is the chirp length (or in case of segmented signal whole cycle duration) and $t_\mathrm{s}$ denotes time within a single chirp ($0 \leq t_\mathrm{s} \leq T_\mathrm{ch}$).
Substituting (\ref{eq:tau2}) into low-frequency part (\ref{eq:fm4}) leads to a very complex equation.
However, according to \cite{suleymanov2016}, most of its terms can be neglected, with result being
\begin{equation}
  s(t_\mathrm{s}, n) = \frac{A^2}{2} \cos\left(\frac{4\pi k_\mathrm{sw} R_0}{c_0} t_\mathrm{s} + \frac{2\omega_c v n}{c_0} T_\mathrm{ch} + \varphi_0 \right),
  \label{eq:fb2}
\end{equation}
where $\varphi_0$ is a phase shift given by the initial distance to a target.
It is clear that the first element describes predominantly the distance to a target, and the second one describes the speed of a target.
We can also see that speed will not affect the beat frequency in a single spectrum but will lead to a phase shift across multiple spectra \cite{suleymanov2016}.

In order to calculate the Doppler shift frequency,
\begin{equation}
  f_\mathrm{d} = \frac{2f_\mathrm{c}v}{c_0},
  \label{eq:Doppler2}
\end{equation}
where $f_c$ is the center frequency, a 2D Fourier transform can be used.
First, an FFT is run on each individual chirp, and then another FFT is applied to these individual outputs in order to determine the phase shift.
Given that the FFT spectrum is calculated from complex data, both halves of the spectrum contain useful information.
After applying \verb|fftshift|, we get a spectrum from negative radial speeds (moving away from the radar) to positive (moving towards the radar) with zero in the middle.
This will lead to a so-called range-Doppler map, which on one axis contains information about speed and on the second axis contains information about the distance of the target.

Speed resolution is derived from the number of chirps $N$ we are analyzing and their length $T_{\mathrm{ch}}$ as \cite{suleymanov2016}
\begin{equation}
  \Delta v = \frac{c_0}{2f_c} \frac{1}{NT_{\mathrm{ch}}}.
  \label{eq:Doppler3}
\end{equation}
The maximal speed is dictated by how large of a phase shift we can measure without ambiguity, that is $\pm \pi$.
From (\ref{eq:fb2}), we can formulate the maximal speed measurable as
\[
  v_\mathrm{max} = \frac{c_0}{4f_c T_\mathrm{ch}},
\]
according to \cite{fmcwSpeed}.
But given the nature of FFT, this speed applies to the negative side of the spectrum -- that is, for targets moving away from the radar.
In the case where the target is moving towards the radar, the speed limit is smaller by a single speed bin width

\section{Radar Equation}

Fundamental to all radar systems is the so-called radar equation.
This formula establishes a relation between the transmitted/received power, the Radar Cross Section (RCS) of the target, and other system parameters to the maximal range of the radar.
It can be written as
\begin{equation}
	R_\mathrm{max}^4 = \left(\frac{P_{\mathrm{CW}}G_\mathrm{T}G_\mathrm{R}\lambda^2}{(4\pi)^3 L k T F_\mathrm{R}B_\mathrm{Ro}(SNR_\mathrm{Ro})} \sigma_T\right),
	\label{eq:radar_eq}
\end{equation}
where $P_\mathrm{CW}$ is the average system power in watts, $G_\mathrm{T}$ and $G_\mathrm{R}$ gain of transmitting and receiving antennas, $\sigma_T$ is the radar cross section of a target, $\lambda$ is wavelength, $L$ is the system loss, $k$ is the Boltzmann's constant, $T$ is the effective temperature of the system in Kelvin, $F_\mathrm{R}$ is the receiver noise figure, $B_\mathrm{Ro}$ is the receiver bandwidth and $SNR_\mathrm{Ro}$ is required SNR \cite{jankiraman2018}.

Knowing all parameters, or calibrating the system based on a known reference, we can calculate the target's RCS.
This value gives us a much clearer understanding of the target as opposed to just displaying the power received or its logarithm.
This is due to RCS being a constant value for a given target and its orientation, regardless of the distance \cite{richards2022}.

\section{Angle of Arrival/Spatial Information}

Commonly, in order to get spatial information, radars rely on multiple RX antennas.
This allows for the estimation of the angle of arrival (AoA) of the target by analyzing phase differences between signals received on different antennas \cite{suleymanov2016}.
However, usually, only a single linear series of RX antennas is employed; therefore, only one angle can be estimated.

More complex MIMO systems employ not only multiple RX antennas but also multiple TX antennas.
Multiple TX antennas enable beamforming, which is the process of steering the radar beam in a specific direction using positive interference.
If antennas are still arranged in a linear array, this only makes the angle of estimation more accurate by effectively creating virtual RX antennas.
However, if a 2D arrangement of antennas is used, the system can estimate both azimuth and elevation angles \cite{sandeep2018}.

While these systems allow for superb performance, they are also very expensive and require a lot of processing power.
Therefore, this thesis works with a simpler and older solution: a system with a single RX antenna and TX antenna, where the radar is pointed in a given direction mechanically.
This approach is not only cheaper but also allows for the gathering of information about the whole 3D space with just a single radar.

\section{CFAR}

CFAR is a simple algorithm that enables basic target detection in noisy radar data.
For each range bin, its neighborhood's power level is calculated.
This neighborhood is separated by a number of guard cells from the cell under test, which do not partake in the calculation.
If the bin under test is greater than the scaled average power level of the neighborhood, we can assume that there is a target present \cite{jankiraman2018}.

There are many different variations of CFAR, each with its own advantages and disadvantages.
What was described is a basic cell averaging CFAR (CA-CFAR).
This algorithm works best in homogeneous environments, where the noise level is relatively constant across the neighborhood.
In cases where this cannot be assumed, for example, CFAR with the greatest of the neighborhood (CAGO-CFAR) can be used.
This algorithm works by taking the maximum value of the neighborhood and comparing it to the bin under test instead of the mean \cite{rohling1983}.

\chapter{\sirad}

Indie Semiconductor's \sirad is a FMCW radar system development kit designed primarily for automotive applications.
Out of the box, it offers two headers a 24~GHz and a 122~GHz both based on ICs from Indie Semiconductor (TRX-024-007 and TRA-120-001, respectively).
Both are strictly SISO transceivers with two antennas: one for receiving and another for transmitting.
So azimuth estimation is not possible out of the box.

\begin{figure}[h!]
  \centering
  

  \caption[\sirad  24~GHz configuration \cite{siradMANOld}]{\sirad  24~GHz configuration \cite{siradMANOld}}
  \label{fig:sirad}
\end{figure}

Direct communication with the radar header is not possible, or at least, the communication interface is undocumented.
Instead, there is always an intermediary in the form of an STM32 Nucleo series microcontroller.
To this microcontroller, the user connects either directly with UART over USB or with WiFi, enabled by an on-board ESP32.
Both are relatively low-bandwidth communication methods, with the serial maxing out at a baud rate of 1,000,000 \cite{siradMAN}.

\begin{figure}[h!]
  \centering
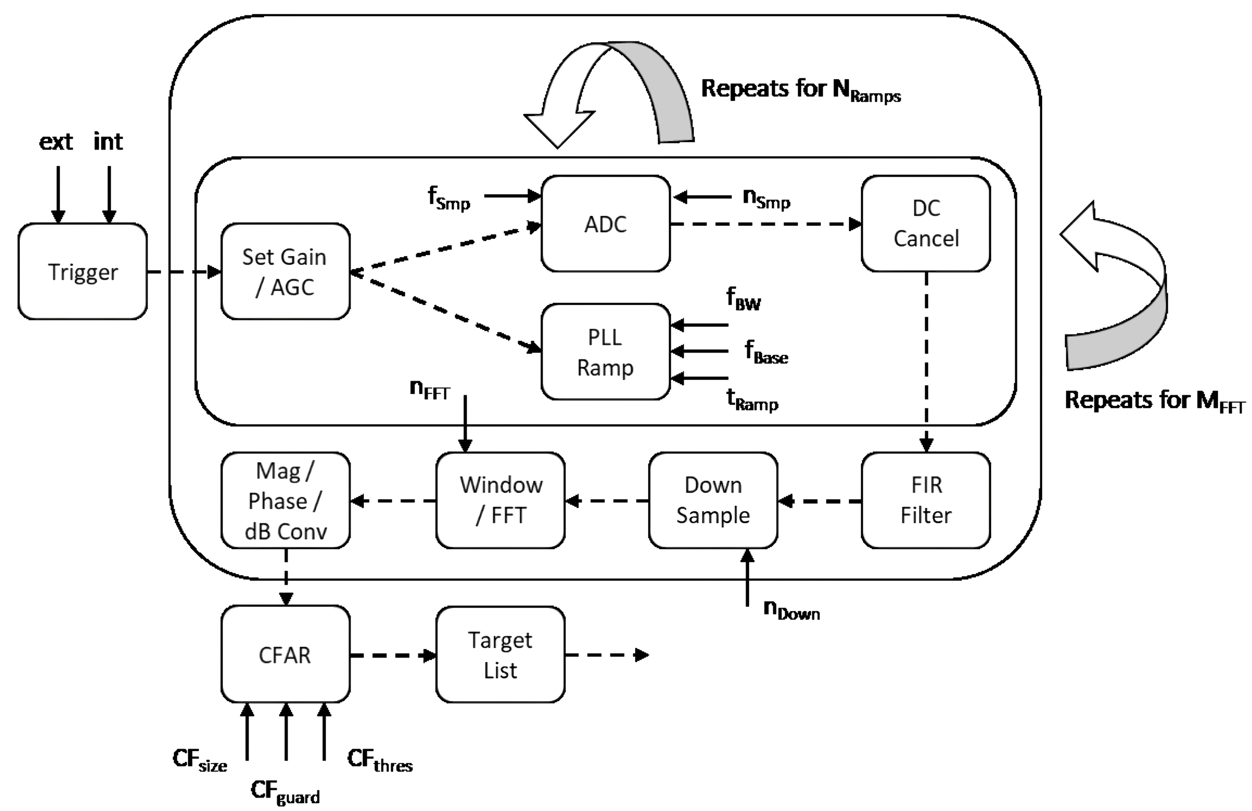
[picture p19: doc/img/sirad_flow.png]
  
  \caption[Flow of Radar Measurement on \sirad \cite{siradPRO}]{Flow of Radar Measurement on \sirad \cite{siradPRO}}
  \label{fig:siradFlow}
\end{figure}

The devkit is designed for easy integration into existing projects; however, this unfortunately poses limitations for this thesis.
In normal operation, the radar system functions as a black box (processing schema shown in \ref{fig:siradFlow}), implementing its own filtering, FFT, and CFAR algorithms while only reporting a target list to the user.

This entire sequence started either by internal trigger or with external input (Be it via a GPIO pin or UART.).
Once the trigger is received, the device carries out a user-configured number of chirps.
Each with length determined by the number of sampling steps and the ADC sampling time as follows
\begin{equation}
  t_\mathrm{ramp} = \frac{t_\mathrm{ADC} \cdot  (N_\mathrm{samples} + 85)}{36\,\, \mathrm{MHz}} \,\, \mu\mathrm{s}.
  \label{eq:sampling}
\end{equation}
The manufacturer recommends keeping $r_\mathrm{ramp}$ around 1~ms for a good SNR \cite{siradPRO}.

SiRad is designed to leverage coherent averaging to improve SNR of the output.
This is achieved by broadcasting multiple ramps in series and averaging the results.
While this technique was found to aid in measurement in a cluttered environments averaging effectively destroys the information about the Doppler shift.
Additionally, due to the devkit's limited computational resources instead of a sawtooth waveform the radar broadcasts a segmented one with significant delays in between \cite{siradPRO}.

The devkit is clearly focused primarily on range measurement with little to no regard payed for speed calculation.
Not only are chirps spaced with large delays (at minimum some 20~ms) but the radar doesn't even maintain constant intervals between chirps.
This is the case even when relying on manual triggering of the radar.
When using radar's self trigger results are even worse.

When measuring reporting interval with 20~ms trigger the radar achieved average time between updates of 20.5~ms with standard deviation of 1.3~ms.
However from time to time they were outliers when report came in only after 30~ms in the worst case or just 16~ms in the best case.
This was on relatively small dataset of 5000 samples.
In order to rule out that the problem isn't only in reporting output signal from the radar was captured by Rohde \& Schwarz FSW26 Signal and Spectrum Analyzer.
By analyzing some 40 samples, broadcasted with the same trigger interval of 20~ms, average time between chirps was 20.7~ms with standard deviation of 0.7876~ms thus proving that broadcast itself is irregular.

Unfortunately as the radar doesn't maintain constant intervals between chirps speed measurement precision is severely limited.
This could be partially mitigated if we knew when the chirp was broadcasted, giving us ability to introduce a correction.
However no such information is provided by the radar.
Thus each chip is timestamped with it's time of arrival which is assumed to be the time of chirp broadcast.
Using this timing information speed spectrum can still be estimated using non-uniform DFT.

According to the radar's manual \cite{siradPRO}, the following equation was used to calculate the width of a single range bin:
\begin{equation}
	\Delta R = \frac{c_0 (N_\mathrm{samples}+85)}{2\cdot BW\cdot NFFT},
  \label{eq:rangeBin}
\end{equation}
where the variable $N$ denotes the number of samples and $NFFT$ the number of DFT points used to calculate the spectrum.
Except the corrective constant of 85 it closely follows the formula (\ref{eq:distance3}).

As for velocity the manufacturer doesn't recommend any formula so (\ref{eq:Doppler3}) was used with $T_\mathrm{ch}$ substituted by the user-chosen trigger period.
However, as the minimal period of chirps is rather high, not to mention the radar doesn't maintain constant intervals between chirps, the velocity measurement is not very practical.
Were we to use 24~GHz header with 25~ms trigger we get maximal speed of 0.124~m/s and on low 8 NFFT steps and the resolution is only $0.031$~ms$^{-1}$.

This lack of performance severely limits the radar's usability with regard to surveillance applications.
Most surveillance radars are designed to monitor dynamic environments, where targets are moving, usually at much higher speeds than the \sirad can measure.
This radar is completely unsuitable for such applications and is mainly applicable to static environments.
For example, in a parking lot, an operator can detect if a car is parked in a given spot or not.
However, besides such binary information about the presence of a target and its distance, not much more can be said.

\section{Outline of the Chosen Configuration }

For the purpose of this project, the devkit was configured to output raw data from the 12-bit ADC in the form of in-phase and quadrature components of the signal.
This allows for more complex processing than if the spectrum was calculated on the radar itself.
However it must be said that regardless of the output format the reported values do not use the full 12-bit range, highest values reported were around $\pm 60$.

Given the unreliability of the radar's internal internal trigger the device was set up to be triggered externally.
In order to not complicate the system too much, trigger over serial line was used.

Another parameter to consider in relation to surveillance application was AGC.
Using it adds two additional ramps that are used solely to set the gain value, leading to some 3 ms delay.
However, a bigger problem is the fact that the radar doesn't report the gain value.
Using AGC could then lead to situations where the weighting of the data is not constant across rotation.
Thus, it was deemed safest to turn AGC off and set the gain manually, depending on how the readings appear after processing.

It is also important to note that the radar system is not well-suited for on-the-fly configuration changes.
Applying a new configuration takes some time, and the radar does not provide any feedback to indicate when a new configuration was applied.
As a result, commonly used techniques such as alternating chirp slope are not feasible.

In regard to the output format, the radar system supports two options: binary and TSV.
Since the output speed does not differ significantly between the two, the primary deciding factor was ease and speed of parsing.
Even when MATLAB is not particularly optimized for parsing binary data, it still processes binary output approximately 40\% faster than human-readable TSV data.

Other parameters, such as sampling frequency and the number of samples, were left to the user to configure.
Setting these strongly depends on which header is used and the environment in which the radar is in.
Thus, making their configuration static wouldn't be a good idea.

\section{24~GHz Header}

The core block of 24~GHz header is a SISO TRX-024-007 transceiver, which integrates low noise amplifier, frequency mixer, filters and VCO into a single package.
It is primarily designed to operate in the ISM band (24.0--24.25 GHz), but also supports an additional ultra-wideband mode with a frequency range from 23 GHz to 26 GHz \cite{siradTRX24}.
On the \sirad there is no distinction made between  those two modes and the user is free to set any bandwidth they want \cite{siradPRO}.
The transmitter output power ranges from 2.5 dBm to 6 dBm, depending on the configuration \cite{siradTRX24}.
A maximal range of 400 m is advertised \cite{siradMANOld}, though in practice only ranges of around 300~m were achieved, with target being a multistory building.

As shown in figure \ref{fig:sirad}, the chip is connected to two microstrip patch antennas.
The patches are arranged in a relatively standard configuration, forming a 6 $\times$ 4 array with spacing approximately equal to half the wavelength at 24 GHz.

Since the manufacturer did not provide any information about the radiation pattern of the array, a simulation was conducted using the CST simulation suite.
Additionally, the manufacturer did not disclose the substrate parameters for the radar board specifically.
Fortunately, the TRX-024-007 datasheet includes a board stack-up for the chip's evaluation board.
It was assumed that the same stack-up would be used: 18 \textmu m copper for the traces and ground plane, with a 250~\textmu m thick Rogers RO4350B substrate \cite{siradTRX24}.

\begin{figure}[ht!]
  \centering
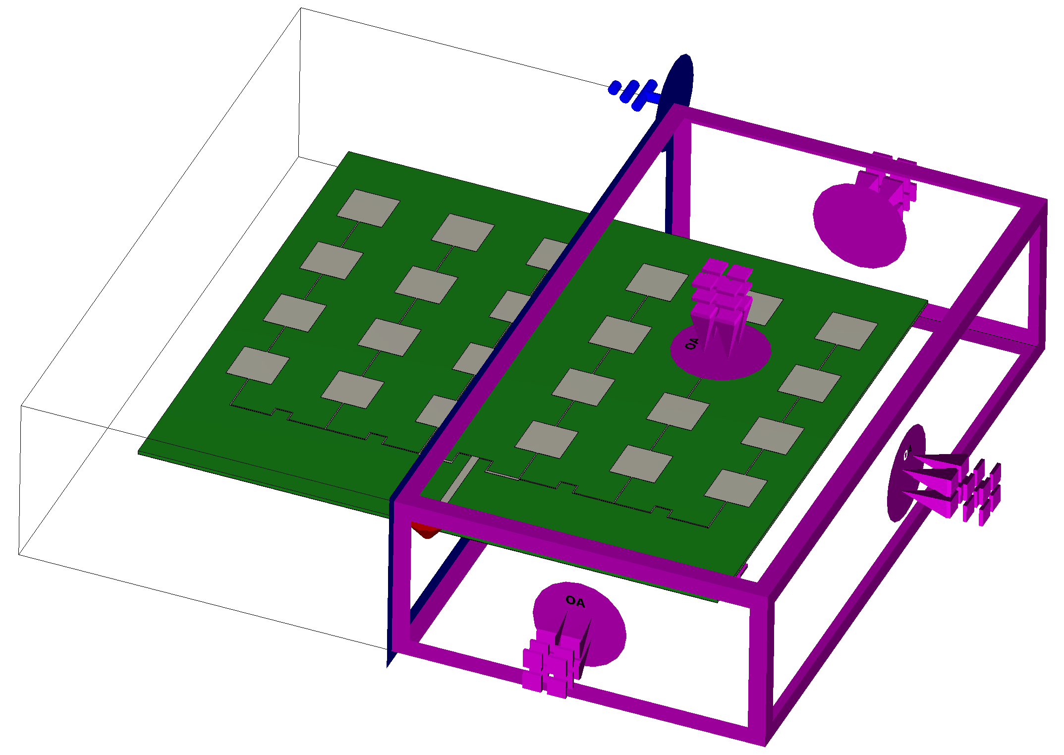
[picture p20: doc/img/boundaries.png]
  
  \caption[Simulated 24 GHz header with boundary conditions showed]{Simulated 24 GHz header with boundary conditions showed}
  \label{fig:boundaries}
\end{figure}

After measuring the dimensions of the array using an optical microscope, the entire array was redrawn in CST Studio.
Figure \ref{fig:boundaries} shows the applied boundary conditions: the antenna was placed in open space, and a  $H_\mathrm{norm}=0$ condition was set along the symmetry plane to speed up the simulation.

After performing a standard time-domain simulation with an excitation signal ranging from 0 to 26GHz, the antenna array exhibited a minimum reflection coefficient $s_{11} \doteq -26.4 \mathrm{~dB}$ at 23.478~GHz with second minimum at 24.518~GHz (Figure \ref{fig:s11}).
The lack of minimum at 24~GHz is likely due neglecting imperfection in the manufacturing process where roughness of the copper traces manifests as a change in the effective dielectric constant of the substrate.

At both frequencies with minimal reflection, a far-field radiation pattern was calculated.
For clarity, only the 24.518~GHz pattern is shown in figure \ref{fig:farfield3d}.
The main lobe width was measured at approximately 16 degrees (Figure \ref{fig:farfield180}) along the 180-degree norm, with a peak gain of 18.6~dBi and side-lobe suppression of -13~dB.
For the 90-degree norm, the main lobe width (Figure \ref{fig:farfield90}) was 30 degrees, with side-lobe suppression of -10~dB.

It's clear that, especially in the 90-degree norm, the beam isn't that narrow.
Thus, this header is not suitable for applications where accurate elevation information is needed.
However, if only a low degree of accuracy is required or a wider field of view would be beneficial, this header is a good choice.
With wider beam  the radar can gather more information about the environment faster compared to one with a narrower beam.
In industry, some surveillance radars are also designed to have a wide beam in elevation, such as some Air Traffic Control radars \cite{kratos} or even some ground radars \cite{blighter}.
Still, usually, solutions such as low/high beam switching are preferred instead of relying purely on a wide beam \cite{wolfBeam}.

\begin{figure}[h!]
  \centering
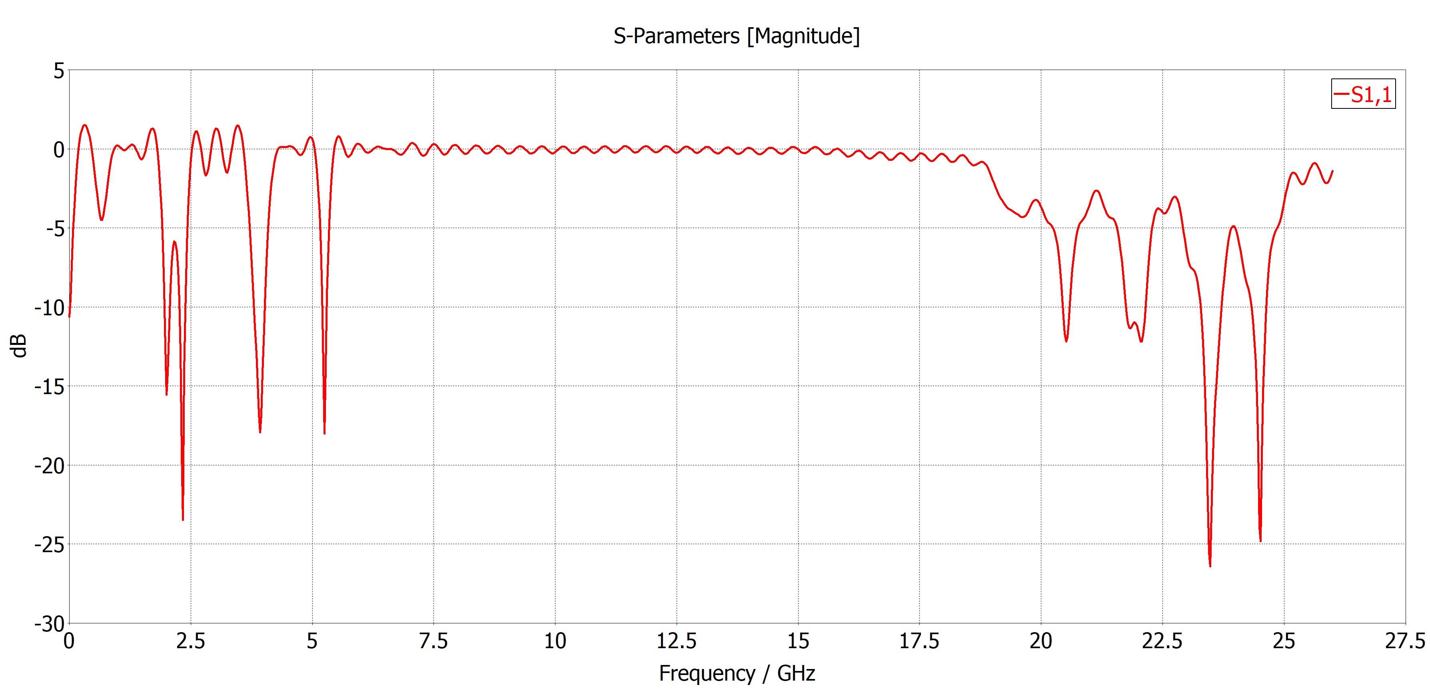
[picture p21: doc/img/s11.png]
  
  \caption[$s_{11}$ parameter of the 24~GHz header]{$s_{11}$ parameter of the 24~GHz header}
  \label{fig:s11}
\end{figure}

\begin{figure}[h!]
  \centering
  
  \caption[Radiation pattern of 24~GHz header -- 3D view]{Radiation pattern of 24~GHz header -- 3D view}
  \label{fig:farfield3d}
\end{figure}

\begin{figure}[h!]
  \centering
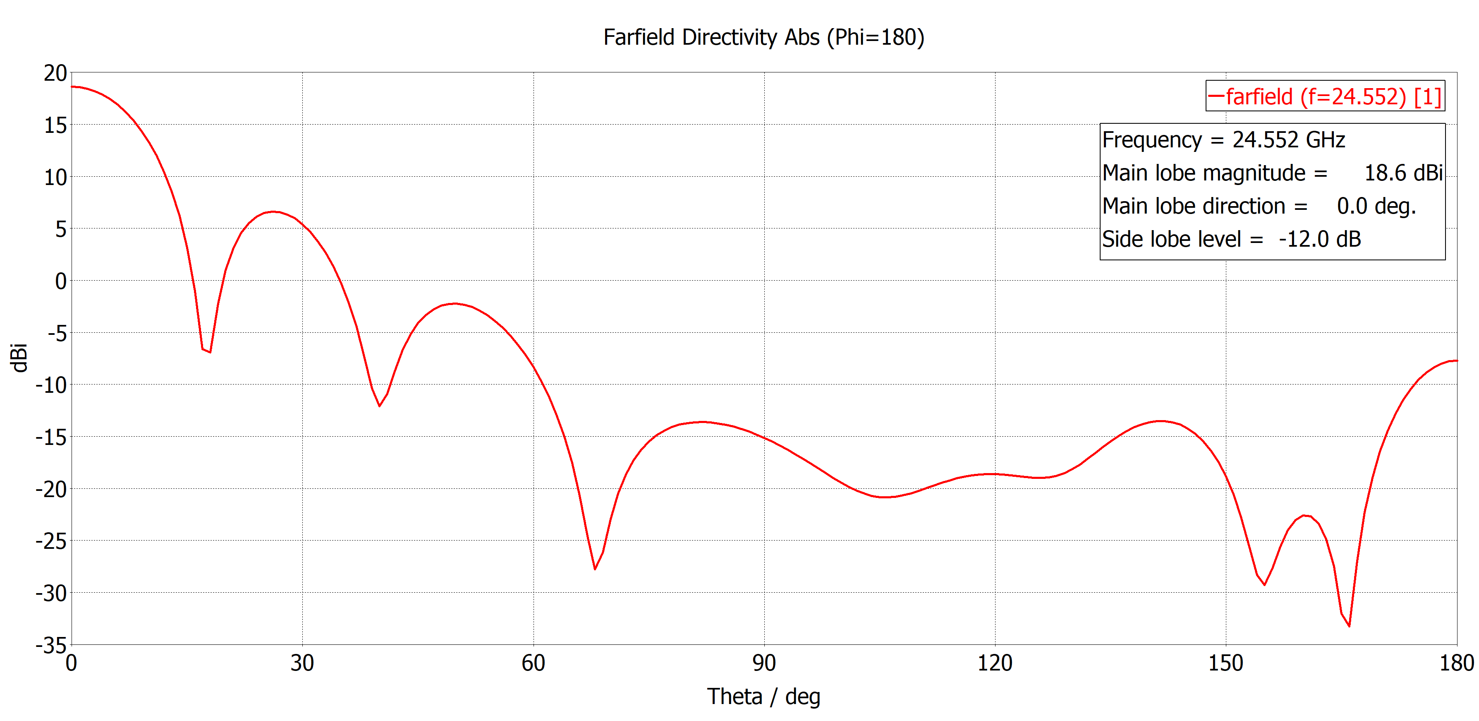
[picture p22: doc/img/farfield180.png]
  
  \caption[Radiation pattern of 24~GHz header -- 180° norm]{Radiation pattern of 24~GHz header -- 180° norm}
  \label{fig:farfield180}
\end{figure}

\begin{figure}[h!]
  \centering
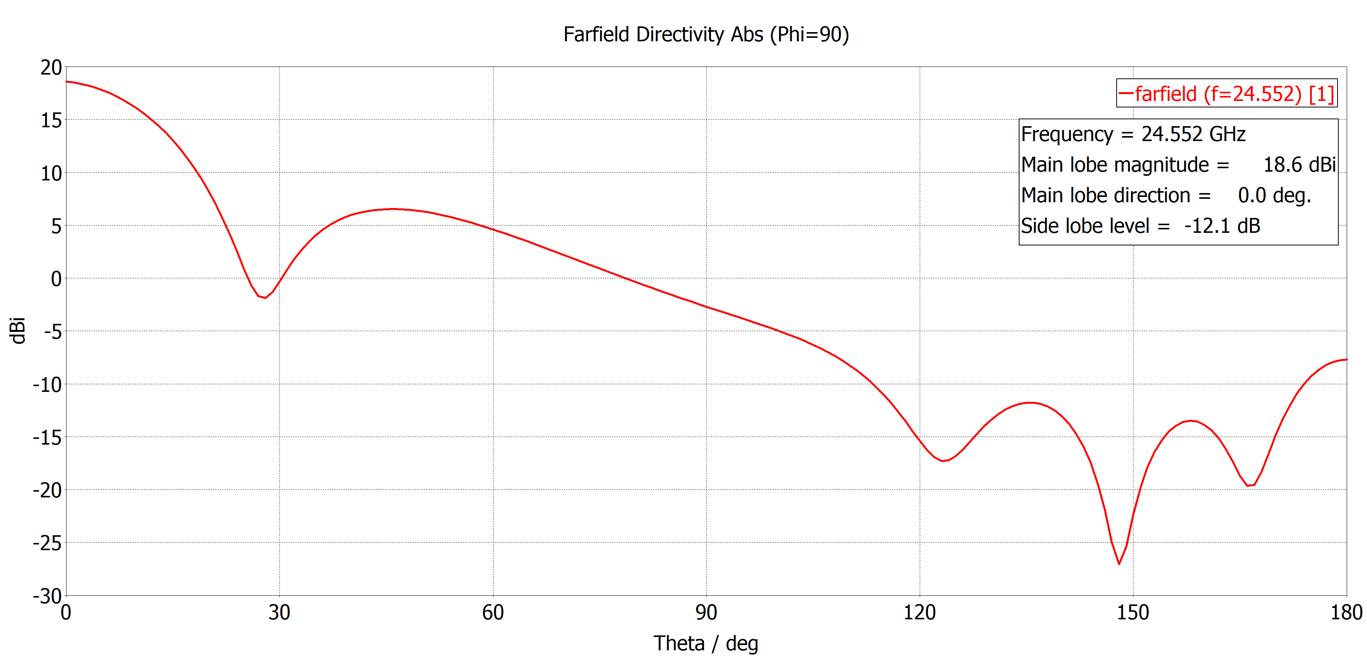
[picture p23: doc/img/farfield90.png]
  
  \caption[Radiation pattern of 24~GHz header -- 90° norm]{Radiation pattern of 24~GHz header -- 90° norm}
  \label{fig:farfield90}
\end{figure}

\section{122~GHz Header}

\begin{figure}[h!]
  \centering
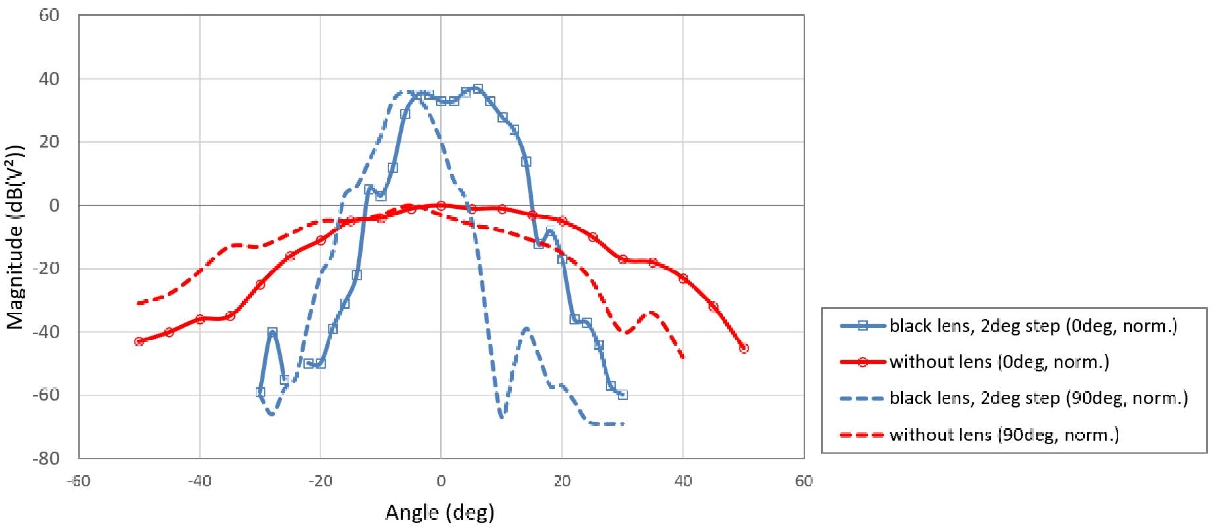
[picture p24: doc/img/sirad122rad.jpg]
  
	\caption[Radiation pattern of 122~GHz header comparison \cite{siradTRX122col}]{Radiation pattern of 122~GHz header comparison \cite{siradTRX122col}}
  \label{fig:sirad122rad}
\end{figure}

The 122~GHz header is based on the TRX-120-001 transceiver, which, in addition to the essential components required for RF transmission and reception, also incorporates two on-chip antennas.
It's designed to operate in the 122-123~GHz band, with an output power ranging from -7~dBm to 1~dBm \cite{siradTRX122}.
The chip is advertised as capable of detecting large targets at distances of up to 40~m \cite{siradMANOld}.

Out of the box performance of the system is quite bad (Figure \ref{fig:sirad122rad}) with the width of the main lobe being roughly $\pm40\text{°}$ in both E-plane and H-plane \cite{siradTRX122}.
However, this can be significantly improved using the supplied collimator lens, reducing the main lobe width to $\pm4\text{°}$ \cite{siradTRX122col} (Figure \ref{fig:sirad122rad}).

\chapter{Rotary Platform}

The following chapter outlines the design process and operational principles of a rotary platform specifically developed for the \sirad radar system.

\section{Platform Construction}

As the platform needs to transmit data from the rotating section to the stationary base a slip ring is required.
Due to the relatively low transmission speed of the radar and the absence of special requirements such as waterproofing, an affordable model, UH3899-01-0810 from Senring, was selected.
It is a classic contact slip ring that features a dedicated USB~2.0 connection along with 8 additional signal wires.
Advertised insertion is less than 2~dB \cite{slipring}.
More problematic than the loss, however, is crosstalk between signal wires when the pitch control stepper motor is running.
This necessitated the addition of a small capacitor to the endstop signal wire to filter out high-frequency noise.

While the USB~2.0 connection does not seem affected by the crosstalk, its connection still isn't ideal.
Without a signal conditioner connected directly to the slip ring output, signal quality is poor enough that a direct connection to the PC is required -- thus, the radar needs to be some 20~cm from the PC.
Even then, depending on the PC's USB port wiring, some ports might exhibit issues.
In addition, the manufacturer opted for a non-standard male-male USB~2.0 connection, requiring a female-female adapter to connect the radar to the slip ring.

Due to the relatively low angular resolution of the radar, high platform precision was not a requirement.
A basic 200-step stepper motor with a step size of 1.8\text{°} was deemed sufficient.
In case the user requires more granular control over the position, it can be facilitated by microstepping.

Similarly, high-speed movement was unnecessary for this application.
As was already outlined, the radar is capable at best of some 50~Hz update rate.
To put things into perspective at low 8~RPM a degree of angle is traversed in 21~ms, thus any faster speed would lead to having less then one sample per degree.
At these speeds, standard 40~mm NEMA17 stepper motors were found to be sufficient.
However if faster rotation or higher levels of microstepping would be needed a stronger motor would be required.
Due to the slip ring's stiffness the motor is already working close to its limits.

Rest of the design is relatively simple.
The slip ring is mounted to a 3D printed base that elevates it slightly above ground.
Stepper motor is then mounted directly under the slip ring, with a shaft connecting it to the rotating base.
The connection is secured using long M4 set screws that pass through the base, through the slip ring, and hold the shaft in place.
A 3D-printed housing serves only as a centering guide and is not under any load from the shaft connection.

The rotating section features a simple A-frame design that elevates the radar, which is mounted on two ball bearings, allowing it to tilt freely.
To control the pitch, a second stepper motor is mounted on the rotating platform and linked to the radar via a 2:1 down-gearing ratio using a standard 8~mm belt.
An optical endstop, used for homing the platform, is attached to the second support strut.

Unfortunately, while the design offers some ability to tension the belt, in the currently printed configuration the adjustment range is not sufficient to fully tension the belt.
While slippage is not a problem, there is some slack in the radar's tilt.
However, as the radar's capabilities in the pitch direction are not particularly high, it was decided not to reprint the whole assembly, but only to fix the issue in supplied 3D models.

Given that mechanical stresses are minimal, most parts can be 3D-printed using standard PLA filament.
The only non-3D-printed components are the screws, shaft, bearings and stepper motors.
The final assembly (Figure~\ref{fig:side_by_side}) measures approximately 36~cm in height and has a footprint of roughly $20\times20$~cm.

\begin{figure}[h!]
  \centering
  \begin{subfigure}[b]{0.55\textwidth}
    \centering
    
    \caption{3D render}
  \end{subfigure}
  \hspace{0.05\textwidth} % Adjust spacing
  \begin{subfigure}[b]{0.35\textwidth}
    \centering
    
    \caption{Photo}
  \end{subfigure}
  \caption{Form of the final assembly}
  \label{fig:side_by_side}
\end{figure}

\subsection{Platform Electronics}

The electronic side of the platform is relatively simple.
Only two problems needed to be tackled: driving the stepper motors and implementing a homing mechanism.

Given the platform cannot generate any significant momentum that could potentially lead to skipping steps a basic stepper driver without feedback control was deemed sufficient.
In the project A4988 stepper driver was chosen due to its low cost, up to 1:16 microstepping capabilities, and basic current control.
A minor drawback of it is the lack of any feedback from a driver to the microcontroller, including stall detection \cite{a4988}.

Since the number of components is quite low and there aren't any special requirements for the circuit, just a simple prototyping board  (Figure~\ref{fig:circuit}) was used instead of designing a custom PCB.
This decision also makes it easier to replace a driver in case of failure.
Or even enables an upgrade path via more modern chips, such as the TMC2208 or TMC2209 as their devkits are pin-compatible with the A4988 \cite{a4988_sound}.
This might be necessary in use cases where the platform's volume level would be a serious problem.
The A4988 produces a rather noisy driving signal and more modern drivers exhibit up to 20~dB lower noise levels \cite{a4988_sound}.

For homing implementation, two potential solutions were considered: Hall effect sensors and optical gates.
Hall effect sensors offer the advantage of angle sensing, allowing correction for positional drift during operation; however, they require precise alignment.
If the Hall effect sensor is not perfectly placed along the axis of rotation, calibration becomes necessary \cite{hall}.
While feedback would be beneficial, the microcontroller already tracks each step taken by the motor during normal operation, making it possible to determine the platform's position purely in software.
Thus, for simplicity and ease of integration, optical gates were selected.

The system is controlled by an ESP32 microcontroller.
The ESP32-C6 version was chosen due to the author's extensive experience with this particular model.
Still, since the system does not require specialized peripherals or high processing power, most other microcontrollers could have been used instead.

\begin{figure}[h!]
	\centering

	\caption[Driving circuit of the platform]{Driving circuit of the platform}
	\label{fig:circuit}
\end{figure}

\section{Platform Software}

As already stated the platform is controlled by an ESP32 microcontroller.
There are two main frameworks available for programming the ESP32: Arduino and ESP-IDF.
As Arduino integration on ESP32 is rather poorly written and is primarily designed for much simpler projects, that do not leverage ESP32's capabilities, the ESP-IDF framework was chosen.
The code needs to handle three main tasks - process incoming commands, control the stepper motors and report their position.

Given its adoption as an industry standard for controlling similar machines, G-code over serial was a natural choice for the platform's communication format.
Beyond the basic functionality of moving steppers a given number of steps, the platform needed to support additional features to reduce the user's manual control burden.
These include things such as defining movement limits, absolute/relative positioning modes, spindle mode (That is continuos rotation for a infinite number of steps.) or automatic homing.
Lastly, in order to offload platform management from the PC the platform needed to support a programming interface.
User should be able to send an entire choreography of movements to the platform at once, after which the platform should execute it without any further input from the user.
Only providing feedback about the current position.

To maximize efficiency in processing commands and ensure accurate stepper motor control, the program workflow was divided into three distinct layers, as illustrated by figure~\ref{fig:code_diag}.
The commonly used two-component architecture -- where one component handles communication and command parsing, and the other manages execution -- was deemed unsuitable for this use case.
Such an approach would complicate integration of a programming interface and require just-in-time processing of commands, which could lead to performance issues.

In the chosen architecture, the degree of abstraction decreases with each successive layer, simplifying processing at each step.
This design allows the final layer to operate with maximum efficiency, where the transition from one command to the next is nearly instantaneous.

It is necessary to note that the platform does not store any permanent configuration, including microstepping settings.
This approach was taken because the platform does not offer any easy way to display the current settings and is expected to be operated only from a computer application.
Thus, instead of needing to keep track of which settings are on the PC and which are stored on the platform, a simpler approach was taken.

\begin{figure}[h!]
  \centering

  \begin{tikzpicture}[scale=0.9, node distance=1.5cm]

    % Layer headers
    \node (comm_layer) [layerheader] at (0, 0) {Communication Layer};
    \node (app_layer) [layerheader] at (6, 0) {Application Layer};
    \node (hal_layer) [layerheader] at (12, 0) {HAL Layer};

    % Communication Layer
    \node (comm_start) [startstop, below of=comm_layer, yshift=-0.3cm] {Start};
    \node (wait_serial) [process, below of=comm_start] {Wait for serial data};
    \node (parse_gcode) [process, below of=wait_serial] {Parse G-code};
    \node (parse_success) [decision, below of=parse_gcode, align=center, yshift=-1.3cm] {Parsing\\ Successful?};
    \node (store_command) [process, below of=parse_success, align=center, yshift=-1.8cm] {Store command\\ queue ? program};
    \node (send_response) [process, below of=store_command,yshift=-0.25cm] {Send response};

    % Arrows in Communication Layer
    \draw [arrow] (comm_start) -- (wait_serial);
    \draw [arrow] (wait_serial) -- (parse_gcode);
    \draw [arrow] (parse_gcode) -- (parse_success);
    \draw [arrow] (parse_success.east) -- ++(1, 0) |- (send_response.east) node[midway, left, yshift=+0.25cm] {No};
    \draw [arrow] (parse_success.south) -- ++(0, -0.5) -| (store_command.north) node[midway, right, yshift=+0.05cm] {Yes};
    \draw [arrow] (store_command) -- (send_response);
    \draw [arrow] (send_response.west) -- ++(-0.8, 0) |- (wait_serial.west);

    % Application Layer
    \node (app_start) [startstop, below of=app_layer, yshift=-0.3cm] {Start};
    \node (update_position) [process, below of=app_start] {Update position};
    \node (check_queues) [decision, below of=update_position, yshift=-1.3cm] {Queues full?};
    \node (load) [process, below of=check_queues, align=center, yshift=-1.5cm] {Load command \\ queue ? program};
    \node (process_command) [process, below of=load,yshift=-0.25cm] {Process command};
    \node (store_command) [process, align=center, below of=process_command] {Add command \\ to stepper queue};

    % Arrows in Application Layer
    \draw [arrow] (app_start) -- (update_position);
    \draw [arrow] (update_position) -- (check_queues);
    \draw [arrow] (check_queues.east) -- ++(1, 0) |- (update_position.east) node[midway, left, xshift=0.2cm, yshift=+0.25cm,xshift=0.2cm] {Yes};
    \draw [arrow] (check_queues.south) -- ++(0, -0.5) -| (load.north) node[midway, right, yshift=+0.1cm] {No};
    \draw [arrow] (load.south) -- ++(0, -0.5) -- (process_command.north);
    \draw [arrow] (process_command) -- (store_command);
    \draw [arrow] (store_command.west) -- ++(-0.5, 0) |- (update_position.west);

    \node (hal_start) [startstop, below of=hal_layer, yshift=-0.3cm] {Start};
    \node (wait_queue) [process, below of=hal_start] {Wait on queue};
    \node (execute_command) [process, below of=wait_queue] {Execute command};
    \node (wait_command) [process, below of=execute_command] {Wait on command};
    \node (update_info) [process, align=center, below of=wait_command] {Update last \\command};

    % Arrows in HAL Layer
    \draw [arrow] (hal_start) -- (wait_queue);
    \draw [arrow] (wait_queue) -- (execute_command);
    \draw [arrow] (execute_command) -- (wait_command);
    \draw [arrow] (wait_command) -- (update_info);
    \draw [arrow] (update_info.west) -- ++(-0.5, 0) |- (wait_queue.west);

  \end{tikzpicture}

  \caption[Program flow diagram]{Program flow diagram}
  \label{fig:code_diag}
\end{figure}

\subsection{Communication Layer}

The communication layer processes incoming data over the serial line.
Its efficient handling is facilitated with the aid of RTOS queues.
Upon receiving a command, the string is parsed and either pushed to a queue to be executed later or added to a program declaration, in case the user is currently writing a program.
Some special commands, such as those for emergency shut-off, are executed immediately.
For a complete overview of supported commands consult Appendix~A.

Immediately after parsing, a response is sent to the user confirming whether the command was parsed correctly or not.
However, as the communication layer does not and cannot check the command within the context of all previous commands, it is possible that a command will be parsed correctly but its execution will fail in the application layer.

\subsection{Application layer}

The application layer performs two primary functions: tracking the current device position and preparing commands to be sent to the stepper motors.
Aside from the current position, the program also keeps track of the end position of the last scheduled command.
Thanks to this, the application layer is able to make all necessary calculations to facilitate absolute positioning or enforce movement limits.

A key departure from standard G-code interpreters, such as \cite{duet}, is how the platform handles single-axis move commands.
When a move command targets only one axis, the other axis remains free to read the next command and begin its execution.
If this behavior is undesirable, the user must issue commands for both axes simultaneously.
In relative positioning mode, a zero value results in no motion; in absolute positioning mode, the command must specify the current position to prevent movement.

This behavior is a necessary side effect of the spindle regime, which typically can only be toggled on/off and cannot act as a stepper \cite{duet}.
Another consequence of spindle mode is the requirement for separate positioning modes for each axis.
Continuous rotation prevents calculating a move’s end position, making it impossible to compute commands in absolute positioning, thus necessitating relative positioning.
However, it would be rather restrictive to force the user to use relative positioning on the second axis; therefore, the positioning modes are independent.

To support other possible applications, a manual override mode was also implemented.
This enables the user to manually push a move command directly to the stepper queues, totally skipping the application layer.
The primary use case for this mode is to allow tracking of targets or use in other applications that require real-time control over the platform.
However, user must keep in mind that in this regime, no limits are enforced and the platform operates strictly in relative positioning mode.

\subsection{HAL Layer}

The final layer manages stepper motor control and provides the application layer with essential data for position calculations.
In its loop, the program waits for the next command in the stepper queue.
Upon receiving a command, it sets up execution, waits for one or both steppers to complete their movement, and then proceeds to the next command.
Since limit and absolute positioning calculations are handled in the application layer, the whole routine remains highly efficient -- the layer just moves stepper a given number of steps, or let's it rotate in case of spindle mode.

The main challenge was the generation of precise PWM signals (used to control stepper motor drivers) and stopping the signal generation after a specific number of steps.
As generating a PWM signal in software is impractical, dedicated ESP32C6 peripherals needed to be leveraged.
There are two main options for this task: Remote Controlled Transceiver (RMT) and Motor Control Pulse Width Modulation (MCPWM) combined with Pulse Counter (PCNT).
While RMT allows smooth PWM frequency adjustments, it has several drawbacks: for example, generating a specific number of pulses is supported only on newer ESP32 models \cite{gitRMT}, synchronization is restricted to its proprietary API, and there is no straightforward way to track progress during a move \cite{espRMT}.

For these reasons, combination of MCPWM and PCNT was chosen.
MCPWM handles pulse generation, while PCNT counts steps, enabling easy control over movement and providing a robust API for step count tracking \cite{espPCNT}.
The only limitation is the PCNT’s 15-bit counter, which caps the maximum steps per move at $\pm$32,767.

\subsubsection{Performance of the HAL Layer}

Table \ref{tab:performancepwm} illustrates the stability of PWM generation by the MCPWM module at various speeds.
Measurements were conducted using a Saleae Logic Pro 16 logic analyzer, with no microstepping enabled.

The results show that frequency deviation is minimal, though the generated speed is consistently marginally faster than the target and the error increases slightly at higher speeds.
Nevertheless, when measuring the time for 24,000 steps at 120~RPM, the relative error in time duration (or speed) was only $\varepsilon = -0.004\%$, demonstrating excellent accuracy.

\begin{table}[h!]
  \centering
  \caption[Stability of PWM generation]{Stability of PWM generation}
  \begin{tabular}{| m{2cm} || m{2.5cm} | m{2.5cm} | m{2.5cm} | m{2.5cm} |}
    \hline
    RPM & $f_{\mathrm{desired}}$ (Hz) & $f_{\mathrm{low}}$ (Hz) & $f_{\mathrm{high}}$ (Hz) & $f_\mathrm{avg}$ (Hz) \\
    \hline
    10  & 33.334                      & 33.334                  & 33.334                   & 33.334                \\
    30  & 100                         & 100                     & 100.003                  & 100.002               \\
    60  & 200                         & 200                     & 200.01                   & 200.004               \\
    120 & 400                         & 400                     & 400.02                   & 400.007               \\
    \hline
  \end{tabular}
  \label{tab:performancepwm}
\end{table}

\begin{figure}[h!]
  \centering
  
  
  \caption[Moment of change between commands with 120RPM and 60RPM]{Moment of change between commands (120RPM $\Rightarrow$  60RPM)}
  \label{fig:switching}
\end{figure}

An attempt was made to also measure the delay between switching commands, as displayed in figure~\ref{fig:switching}.
The results indicate that the delay between commands is imperceptible.
Similar outcomes were also observed for other command combinations.

This demonstrates the efficiency of the HAL layer in managing stepper motor control and transitioning seamlessly between commands.
As long as the stepper queues are supplied with commands in advance, the platform can operate without noticeable interruptions.

\chapter{Control Application}

As previously stated, the control application for the whole system is written in MATLAB.
There are two main parts to it: one is managing the platform and the other for processing radar data.
Alongside these, there are some shared components, such as the preferences menu.

\section{Main Window}

Upon starting the application, the user is presented with the main window (Figure~\ref{fig:main_window}).
This window is primarily used to display radar data and control the basic functionality of the application.
On the sidebar, the user can enable serial connections to the radar and the platform, pause processing, save the current visualization to JPG, and stop the platform in case of an emergency.
Lastly, the top bar allows access preferences and the platform control interface.

\begin{figure}[h!]
  \centering
  
  \caption[Main application window]{Main application window}
  \label{fig:main_window}
\end{figure}

\subsection{Application Configuration}

As this thesis concerns itself with a rather generic implementation of a surveillance radar system, the application is designed to be as flexible as possible.
For this purpose, a GUI menu was designed to enable configuration of all important elements -- configuring the platform, radar, data processing, and data visualization.
However, it is necessary to point out that, given the extensive configuration options, the user is expected to have some knowledge about the subject to achieve satisfactory results.
Firstly, configuration options are not checked against each other to verify if they are mutually exclusive.
For example, for speed calculation, ramp averaging must be turned off, but as things stand, the application will allow the user to continue even with it enabled.
Secondly, configuration of components such as CFAR or DBSCAN strongly depends on bandwidth, number of samples, FFT point count, and other parameters.
A CFAR guard parameter of 3 might be too small on a 5~GHz bandwidth with a single range bin width of 50~mm, but with $BW=500$~MHz it could be way too large.
To aid in choosing correct parameters, the application provides some basic information, like the dimensions of the bins.
Still, it is up to the user to make the final decision.

Figure~\ref{fig:preferences} shows the preferences menu; as one can see, there are four main sections.
The first configures serial port connections to the radar and the platform.
The second section handles configuration of the platform, followed by a section designated for radar configuration.
The last section configures how the data are processed and via which method they are visualized.

\begin{figure}[h!]
  \centering
  
  \caption[Preferences menu]{Preferences menu}
  \label{fig:preferences}
\end{figure}

User preferences are stored in an INI file in a directory whose path depends on the operating system used—\texttt{\%APPDATA\%/Local/fmcw/fmcw.conf} on Windows and \texttt{\$HOME/.config/fmcw/fmcw.conf} for Unix-based systems.
As INI format is easily human-readable, it is possible to edit the file directly.

\section{Platform Control Interface}

It is necessary to emphasize that the platform control is entirely independent of the radar.
The user loads a program onto the platform and starts its execution.
From then on, the application only processes current position reports coming from the platform.
There is no feedback from the radar to the platform based on processed data, although, as the platform enables direct access to the stepper queues, it would be possible to implement such feature.
Nor does processing take into account which movements comprise the platform's current program.

In the preferences menu, the user can configure static offsets to the platform with the \texttt{Pitch offset} and \texttt{Yaw offset} options.
This is useful in case the zero position of the platform is not aligned with what the user wants to be zero in the data.
Aside from offset, step count configuration is also available here with \texttt{Step count pitch} and \texttt{Step count yaw}.
Step count takes into account both microstepping and the physical down-gearing ratio.
It is important to note that, as the platform doesn't store the step count in non-volatile memory, this setting is essential to maintain proper operation of the platform.
The step count command is sent to the platform each time it is connected or the configuration is changed.
Lastly, the \texttt{Platform debug} toggle enables full debug output to be visible in the platform control window.

\begin{figure}[h!]
  \centering
  
  \caption[GUI of the platform control]{GUI of the platform control}
  \label{fig:platformControl}
\end{figure}

Managing platform programs is done via a separate window (Figure~\ref{fig:platformControl}).
This interface enables the user to load, edit, and send programs to the platform.
The left sidebar allows the user to load stored programs by clicking on their name.
The middle text boxes are used to edit the program header (top part) and program body (middle part), with the bottom text field being used to display the platform's debug output.
On the right side are buttons that handle basic operations on the program: load, save, store to file, upload, and start.

Commands are written one per line.
Control commands used to denote the start of a program, end of header, and so on are automatically sent to the device when the rest of the program is uploaded.
To validate whether the program was parsed correctly, the user can check the text window at the bottom of the screen, which forwards the platform's debug output.
If the user clicks the store button, the program is stored in the same INI file as the preferences.

Backend side of the platform control is rather straightforward.
After a connection is established, the MATLAB serial interface calls a callback each time a terminator sequence is found in received data.
The received message is then parsed, with debug output being forwarded to the user and positions logged with a timestamp in a circular buffer.
The radar data processing part can then request a list of positions for a given time interval.

Platform control can also emit an event when the platform finds itself close to a predetermined position.
This angle is specified in the \texttt{Reset yaw} option, with a tolerance zone fixed at two degrees on either side.
In order to prevent multiple triggering of the event, the program will only emit it once per 1~s.
When the \texttt{Cube decay} option is set to 'reset', if this event is used to clear stored data after a cycle is completed,

\section{Radar Configuration}

Given that the radar's output is displayed in the main window, there isn't any specialized interface dedicated just to the radar.
Still, in the preferences menu, there are some parameters that can be configured.

The \texttt{Radar frequency} toggle chooses between the 24~GHz and 122~GHz headers.
However, this only affects the configuration sent to the radar; it does not reflash the firmware, which is also necessary.
After the base frequency, \texttt{Radar bandwidth} can also be configured; both positive and negative values are accepted, however manual verification is required to ensure that the radar is working as expected.
While the manufacturer states a 3~GHz limit on the 24~GHz header and 5~GHz on the 122~GHz header \cite{siradPRO}, in practice—especially with the 24~GHz header—achievable bandwidth was usually much lower and its limit was rather inconsistent.

The user can also configure the number of samples per chirp via \texttt{Chirp samples} and the ADC rate with \texttt{ADC ClkDiv}.
These two parameters determine the time of a single ramp, which is calculated with equation~(\ref{eq:sampling}).
Together with gain, ramp time plays a crucial role in maintaining a good signal-to-noise ratio.

The drop-down menu \texttt{Ramp coherent avg} allows the user to pick how many ramps will be averaged together.
However, use of this feature is generally not recommended unless the surrounding environment is too cluttered.
Each ramp adds about 2~ms overhead to the radar's operation and makes speed calculation impossible.

The last parameter is \texttt{Trigger period}, which dictates how often the application will send a trigger command to the radar.
As previously stated, the radar is at best capable of a chirp roughly every 20~ms.

\chapter{Radar Data Processing}

Firstly, it is necessary to outline the inputs and outputs of the entire processing pipeline.
Data are arrive to the application from two sources: serial connections to the radar and to the platform.
These two data streams are then paired together based on timestamps logged when the data are received.
Program then performs user-selected calculations -- components such as CFAR calculation, speed calculation, and so on can be enabled or disabled as needed.
After processing finishes, the output data are stored in a radar cube, a common method for managing radar data that enables easy integration of more complex algorithms in the future \cite{richards2022}.

Given that both CFAR and raw data (that is, individual range-Doppler maps) calculations might be enabled at the same time, the application maintains two radar cubes.
One is a 4D structure with dimensions of fast time $\times$ slow time $\times$ yaw $\times$ pitch, used to store the complete range-Doppler map for each spatial degree.
In this thesis, this structure is only used for visualizing raw data for a given fixed pitch angle or for showing the range-Doppler map for a given yaw and pitch.
Any 3D visualization style of the raw data would be too cluttered and hard to interpret.
The second cube is a 3D structure with dimensions of range $\times$ yaw $\times$ pitch; this one is used to store CFAR output.

In each case, the yaw resolution is fixed at 1 degree, thus the cube is 360° wide.
Given the quality of the radar mounting bracket, the 1.8° resolution of the stepper, and the tightness of the radiation pattern, a 1° resolution was deemed sufficient.
As for pitch, the same resolution was kept, with angles ranging from -20° to +80° being covered.
The lower bound is limited by the radar's mounting bracket, and the upper bound is more or less arbitrary, slightly motivated by trying to prevent the radar from seeing behind itself.

The main complicating factor in the processing was the need to keep the main thread responsive.
The most time-critical responsibility of the main thread is the timely readout of data from the serial ports.
If data cannot be read immediately upon arrival, the assigned timestamps will be incorrect and, therefore, the data will be attributed to a wrong position.
In addition, the GUI becomes quite unresponsive if the main thread's resources are stretched too thin.

To solve this problem, processing heavily leverages MATLAB's Parallel Computing Toolbox, offloading as much as possible to different cores.
Throughout the entire processing pipeline, there are mechanisms for buffering data into larger batches, and if needed, discarding some in case the software is unable to keep up.
Unfortunately, as MATLAB's parallelization capabilities with threads are rather limited -- external language interfaces do not work, nor do certain file or memory mapping functions \cite{matlabParallel} -- the parallelization needed to be done with processes.
This restricts the application to machines with at least 16~GB of RAM, as each process (of which there are three) requires around 2~GB of RAM.

The processing pipeline can be divided into several distinct steps as follows:
\setlist[enumerate]{nosep, topsep=3pt, partopsep=3pt}
\begin{enumerate}
  \item Data acquisition: Data are read, a simple FFT is calculated, and spectra are buffered into a circular buffer.
  \item Data processing: Spectra are retrieved from the circular buffer, paired with positions, and processed.
  \item Cube update: Processed data are buffered into a ping-pong buffer. If the buffer is full, the cube update routine is launched.
  \item Visualization: After cubes are updated, data are visualized.
\end{enumerate}

\section{Data Acquisition}

The basic workflow of this step is shown in figure~\ref{fig:radar_flow}.
The process starts as soon as MATLAB detects a line terminator within the incoming radar data stream.
After the entire frame from the radar is read, the data are timestamped and the I and Q channels are buffered.
The observer \texttt{dataProcessor.m} is then notified and left to retrieve the data when the main thread is free.

After retrieval, the in-phase and quadrature channels are merged to form a complex signal, which is multiplied by a Hann window to prevent spectral leakage.
A basic 1D FFT is then calculated, with the number of points set by the \texttt{Range NFFT} parameter in the preferences.
If the FFT order is larger than the number of samples, zero padding is added.
The resulting spectrum is again buffered in its complex form.
Following this step, the program has in memory multiple FFT spectra -- these can be leveraged to enable range-Doppler map computation.

After the spectrum is stored, the program verifies if the platform has moved.
This check helps save processing resources by avoiding computation of an R-D map that would be immediately overwritten.
After movement is detected, the code then takes all spectra (Except the last one when the platform has changed position.) and launches another processing step in a separate thread.
If the user wishes for processing to always take place (e.g., when verifying radar settings while the platform is static) this check can be skipped by toggling \texttt{Require pos change}.

\begin{figure}[h!]
  \centering
  \begin{tikzpicture}[node distance=1.5cm, scale=0.6]

    % Layer headers
    \node (radar_header) [layerheader] at (0, 0) {radar.m};
    \node (processor_header) [layerheader] at (7.5, 0) {dataProcessor.m};

    % Radar Module
    \node (radar_start) [startstop, below of=radar_header, yshift=-0.3cm] {Start};
    \node (read_serial) [process, below of=radar_start] {Read serial data};
    \node (buffer_raw) [process, below of=read_serial] {Buffer raw data};
    \node (notify) [process, below of=buffer_raw] {Notify observers};

    % Data Processor Module
    \node (proc_start) [startstop, below of=processor_header, yshift=-0.3cm] {On notify};
    \node (read_radar) [process, below of=proc_start] {Read radar data};
    \node (calc_fft) [process, below of=read_radar, align=center] {Calculate FFT\\ Buffer spectrum};
    \node (check_pos) [decision, below of=calc_fft, yshift=-1cm, align=center] {Position\\ changed?};
    \node (get_spectrums) [process, right of=read_radar, xshift=4cm, align=center] {Get spectrums};
    \node (get_positions) [process, below of=get_spectrums] {Get positions};
    \node (cfar_process) [process, below of=get_positions, align=center] {Launch 2D/CFAR\\ processing};
    \node (proc_stop) [startstop, below of=check_pos, yshift=-1.3cm] {End};

    % Arrows for Radar Module
    \draw [arrow] (radar_start) -- (read_serial);
    \draw [arrow] (read_serial) -- (buffer_raw);
    \draw [arrow] (buffer_raw) -- (notify);
    \draw [arrow] (notify.west) -- ++(-1,0) |- (read_serial.west);
    %
    % % Arrows for Data Processor Module
    \draw [arrow] (proc_start) -- (read_radar);
    \draw [arrow] (read_radar) -- (calc_fft);
    \draw [arrow] (calc_fft) -- (check_pos);
    %
    % % Yes branch
    \draw [arrow] (check_pos.east) -- ++(1,0) node[right] {Yes} |- (get_spectrums.west);
    \draw [arrow] (get_spectrums) -- (get_positions);
    \draw [arrow] (get_positions) -- (cfar_process);
    %
    % % No branch
    \draw [arrow] (check_pos.south) -- node[right] {No} (proc_stop.north);

    % \draw [arrow] (cfar_process.south) -- ++(0,-1.7) -| (proc_stop.east);
    \draw [arrow] (cfar_process.south) |- (proc_stop.east);
  \end{tikzpicture}
  \caption{Processing flow - Data acquisition}
  \label{fig:radar_flow}
\end{figure}

\section{Data Processing}

A parallel process takes calculated FFT spectra and their accompanying positions and processes them into a single range-Doppler map and an array with CFAR output.
A basic outline of this step is shown in figure~\ref{fig:feature_flow}.

\begin{figure}[h!]
  \centering
  \begin{tikzpicture}[node distance=1cm, scale=0.5]
    % Main horizontal flow
    \node (processor_header) [layerheader] at (0, 0) {dataProcessor.m};
    \node (start) [startstop, below =of processor_header] {Thread start};
    \node (rcs) [process, right = of start] {Calculate RCS};
    \node (cfar_decision) [decision, below = of start] {CFAR?};
    \node (raw_decision) [decision, right=1cm of cfar_decision] {RAW?};
    \node (speed_decision) [decision, right=1.5cm of raw_decision] {Speed?};
    \node (return) [startstop, below=2.6cm of speed_decision] {Return};

    % CFAR branch
    \node (cfar_proc) [process, below=of cfar_decision, align=center] {Calc\\CFAR};

    % Speed branch
    \node (mock) [process, below left=1.5cm and -0.4cm of speed_decision, align=center] {Use last chirp\\ RCS array};
    \node (fft) [process, below right=1.5cm and -0.4cm of speed_decision, align=center] {2DFFT/\\NUFFT};

    % Connections
    \draw [arrow] (start.east) -- (rcs.west);
    \draw [arrow] (rcs.south) -- ++(0,-1) -| (cfar_decision.north);
    \draw [arrow] (cfar_decision.east) -- node[above] {No} (raw_decision.west);
    \draw [arrow] (cfar_decision.south) -- node[right] {Yes} (cfar_proc.north);
    \draw [arrow] (cfar_proc.east)  -- ++(0.3,0) |- (raw_decision.west);
    \draw [arrow] (raw_decision.south) -- ++(0,0) node[left] {No} |- (return.west);
    \draw [arrow] (raw_decision.east) -- node[above] {Yes} (speed_decision.west);
    \draw [arrow] (speed_decision.south) -- ++(0, -0.5) node[above, xshift=-1cm] {No} -| (mock.north);
    \draw [arrow] (speed_decision.east) -- ++(0, 0) node[above, xshift=+0.5cm] {Yes} -| (fft.north);
    \draw [arrow] (mock.south) -- ++(0,0) |- (return.west);
    \draw [arrow] (fft.south) -- ++(0,0) |- (return.east);

  \end{tikzpicture}
  \caption{Processing flow - Data processing}
  \label{fig:feature_flow}
\end{figure}

In the first step, the last spectrum is converted to values proportional to the radar cross section (RCS) of the target.
Starting with equation~(\ref{eq:radar_eq}), we can see that the target's RCS is proportional to the received power divided by the fourth power of the distance to the target.
Range can be calculated from the manufacturer-supplied equation~(\ref{eq:rangeBin}), and power is proportional to the square of values reported from the radar.
Given that the constants of the radar equation change based on configuration, calibration would be required in order to obtain real RCS values.
However, this calibration is not supported, and thus onward, when referring to RCS we refer to values proportional to the RCS, not the actual RCS of the object.
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

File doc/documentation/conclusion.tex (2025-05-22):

% vim.ft=tex
\chapter*{Conclusion}
\addcontentsline{toc}{chapter}{Conclusion}

The goal of this thesis was to develop a surveillance radar system based on FMCW technology.
This technology enables accurate distance measurements of targets with relatively low power consumption.
Rather than adopting a more conventional MIMO system, a simpler solution was chosen: a single RX and TX antenna, with mechanical beam steering provided by a custom rotary platform.

Using off-the-shelf components and 3D-printed parts, a two-axis rotary platform was designed and constructed.
Despite minor issues with belt tension on the pitch axis, the platform reliably controls the radar’s position in both yaw and pitch, with a standard accuracy of 1.8°, further improvable via microstepping.
Additional features such as automatic homing and rotation limits were implemented for improved usability.
Thanks to its similarity to other G-code-based systems, the platform is readily adaptable to other applications.
Moreover, the platform was designed with capabilities beyond the requirements of this thesis, and during testing it executed commands accurately and without noticeable delay.
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

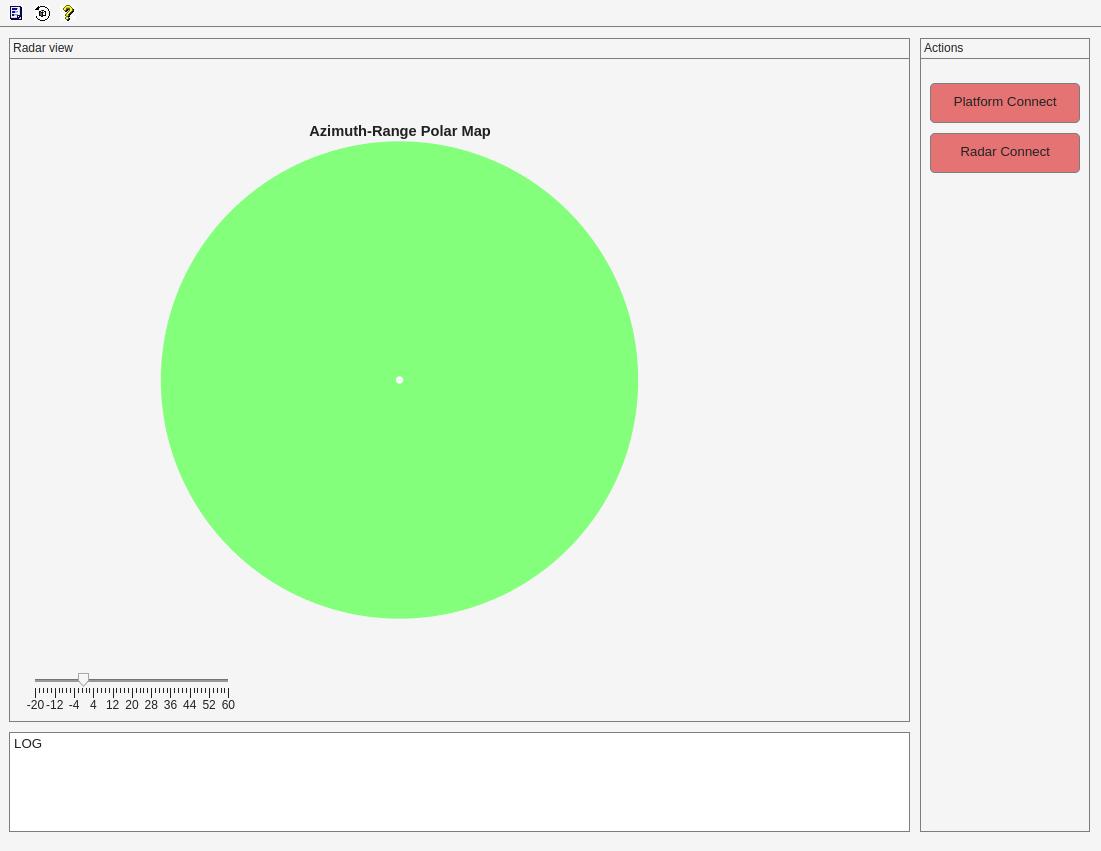
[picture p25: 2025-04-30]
doc/img/main_window.jpg

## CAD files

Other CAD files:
indexing-table/cad/SiDAR mount.f3d
indexing-table/cad/horizontal endstop holder.f3d
indexing-table/cad/rotary base.f3d
indexing-table/cad/slipring mouting bracket.f3z
indexing-table/cad/static base.f3z
indexing-table/cad/superstructure left.f3d
indexing-table/cad/superstructure right.f3d

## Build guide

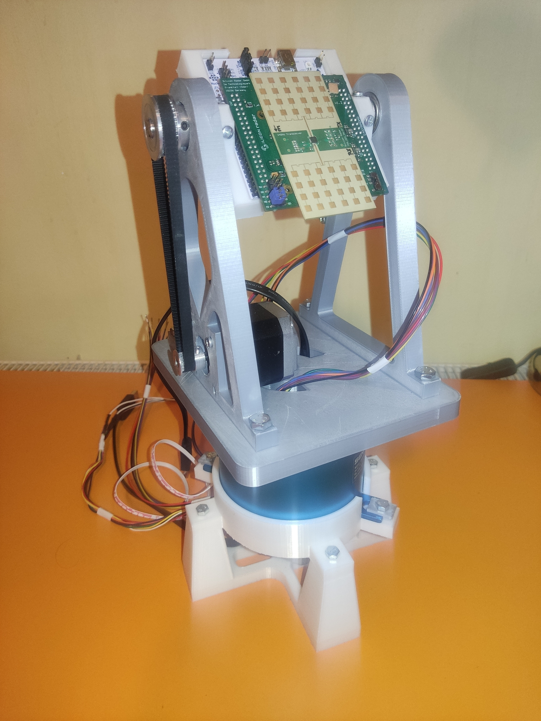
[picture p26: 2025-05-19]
doc/img/assembly_photo_.jpg

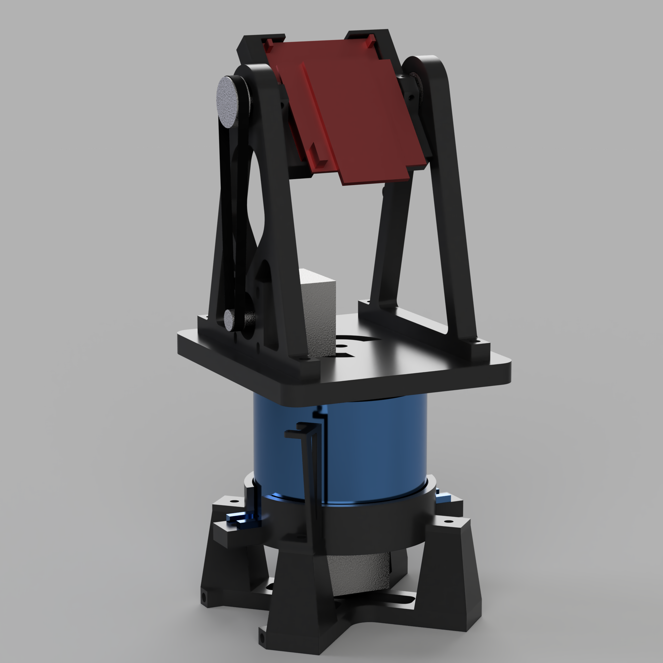
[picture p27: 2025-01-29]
doc/img/whole_assembly_1_crop.png

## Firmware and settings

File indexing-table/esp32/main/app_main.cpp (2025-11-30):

#define TWDT_TIMEOUT_MS  4000

// #include <os_core.h>
#include <esp_event.h>
#include <esp_log.h>
#include <esp_task_wdt.h>
#include <sdkconfig.h>
#include <stdio.h>
#include <comm_endpoint.h>
#include <nvs_flash.h>
#include <stepper_control.h>
#include "esp_task_wdt.h"

extern "C" void app_main(void)
{
	ESP_ERROR_CHECK(esp_event_loop_create_default());

	esp_err_t err = nvs_flash_init();
	if (err == ESP_ERR_NVS_NO_FREE_PAGES || err == ESP_ERR_NVS_NEW_VERSION_FOUND) {
		ESP_ERROR_CHECK(nvs_flash_erase());
		err = nvs_flash_init();
	}
	ESP_ERROR_CHECK(err);

	commEndpoint.setupComm();
	stepperControl.init();
	vTaskDelay(1000 / portTICK_PERIOD_MS);
	stepperControl.parseGCode("G92", 3);
	stepperControl.parseGCode("M92 Y200 P400", 13);




	// NOTE: DEMO CODE
	stepperControl.parseGCode("P90 xx_ro", 14);
	stepperControl.parseGCode("G91", 3);
	stepperControl.parseGCode("G21",3);
	stepperControl.parseGCode("G92",3);
	stepperControl.parseGCode("P29",3); // never stop
	stepperControl.parseGCode("M03 SY5 Y+",10);
	stepperControl.parseGCode("P91", 3);
	stepperControl.parseGCode("P92", 3);

	stepperControl.parseGCode("P90 xx_ti", 14);
	stepperControl.parseGCode("G91", 3);
	stepperControl.parseGCode("G21",3);
	stepperControl.parseGCode("G92",3);
	stepperControl.parseGCode("P29",3);
	stepperControl.parseGCode("M03 SY5 Y+",10);
	stepperControl.parseGCode("P91", 3);
	stepperControl.parseGCode("G0 SP15 P60",11);
	stepperControl.parseGCode("G0 SP15 P-60",12);
	stepperControl.parseGCode("P92", 3);
}

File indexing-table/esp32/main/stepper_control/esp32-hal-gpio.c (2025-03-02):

// Copyright 2015-2016 Espressif Systems (Shanghai) PTE LTD
//
// Licensed under the Apache License, Version 2.0 (the "License");
// you may not use this file except in compliance with the License.
// You may obtain a copy of the License at

//     http://www.apache.org/licenses/LICENSE-2.0
//
// Unless required by applicable law or agreed to in writing, software
// distributed under the License is distributed on an "AS IS" BASIS,
// WITHOUT WARRANTIES OR CONDITIONS OF ANY KIND, either express or implied.
// See the License for the specific language governing permissions and
// limitations under the License.

#include "esp32-hal-gpio.h"
#include "hal/gpio_hal.h"
#include "soc/soc_caps.h"

// It fixes lack of pin definition for S3 and for any future SoC
// this function works for ESP32, ESP32-S2 and ESP32-S3 - including the C3, it will return -1 for any pin

#if SOC_TOUCH_SENSOR_NUM >  0
#include "soc/touch_sensor_periph.h"

int8_t digitalPinToTouchChannel(uint8_t pin)
{
    int8_t ret = -1;
    if (pin < SOC_GPIO_PIN_COUNT) {
        for (uint8_t i = 0; i < SOC_TOUCH_SENSOR_NUM; i++) {
            if (touch_sensor_channel_io_map[i] == pin) {
                ret = i;
                break;
            }
        }
    }
    return ret;
}
#endif

#ifndef CONFIG_IDF_TARGET_ESP32C6
int8_t digitalPinToAnalogChannel(uint8_t pin)
{
    uint8_t channel = 0;
    if (pin < SOC_GPIO_PIN_COUNT) {
        for (uint8_t i = 0; i < SOC_ADC_PERIPH_NUM; i++) {
            for (uint8_t j = 0; j < SOC_ADC_MAX_CHANNEL_NUM; j++) {
                if (adc_channel_io_map[i][j] == pin) {
                    return channel;
                }
                channel++;
            }
        }
    }
    return -1;
}
#endif

int8_t analogChannelToDigitalPin(uint8_t channel)
{
    if (channel >= (SOC_ADC_PERIPH_NUM * SOC_ADC_MAX_CHANNEL_NUM)) {
        return -1;
    }
    uint8_t adc_unit = (channel / SOC_ADC_MAX_CHANNEL_NUM);
    uint8_t adc_chan = (channel % SOC_ADC_MAX_CHANNEL_NUM);
    return adc_channel_io_map[adc_unit][adc_chan];
}

typedef void (*voidFuncPtr)(void);
typedef void (*voidFuncPtrArg)(void*);
typedef struct {
    voidFuncPtr fn;
    void* arg;
    bool functional;
} InterruptHandle_t;
static InterruptHandle_t pinInterruptHandlers[SOC_GPIO_PIN_COUNT] = {0,};

#include "driver/rtc_io.h"

extern void pinMode(uint8_t pin, uint8_t mode)
{

    if (!GPIO_IS_VALID_GPIO(pin)) {
        ESP_LOGE("GPIO-HAL", "Invalid pin selected");
        return;
    }

    gpio_hal_context_t gpiohal;
    gpiohal.dev = GPIO_LL_GET_HW(GPIO_PORT_0);

    gpio_config_t conf = {
        .pin_bit_mask = (1ULL<<pin),                 /*!< GPIO pin: set with bit mask, each bit maps to a GPIO */
        .mode = GPIO_MODE_DISABLE,                   /*!< GPIO mode: set input/output mode                     */
        .pull_up_en = GPIO_PULLUP_DISABLE,           /*!< GPIO pull-up                                         */
        .pull_down_en = GPIO_PULLDOWN_DISABLE,       /*!< GPIO pull-down                                       */
        .intr_type = gpiohal.dev->pin[pin].int_type  /*!< GPIO interrupt type - previously set                 */
    };
    if (mode < 0x20) {//io
        conf.mode = mode & (INPUT | OUTPUT);
        if (mode & OPEN_DRAIN) {
            conf.mode |= GPIO_MODE_DEF_OD;
        }
        if (mode & PULLUP) {
            conf.pull_up_en = GPIO_PULLUP_ENABLE;
        }
        if (mode & PULLDOWN) {
            conf.pull_down_en = GPIO_PULLDOWN_ENABLE;
        }
    }
    if(gpio_config(&conf) != ESP_OK)
    {
        ESP_LOGE("GPIO-HAL", "GPIO config failed");
        return;
    }
}

extern void digitalWrite(uint8_t pin, uint8_t val)
{
	gpio_set_level((gpio_num_t)pin, val);
}

extern int digitalRead(uint8_t pin)
{
	return gpio_get_level((gpio_num_t)pin);
}

static void onPinInterrupt(void * arg) {
	InterruptHandle_t * isr = (InterruptHandle_t*)arg;
    if(isr->fn) {
        if(isr->arg){
            ((voidFuncPtrArg)isr->fn)(isr->arg);
        } else {
        	isr->fn();
        }
    }
}
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

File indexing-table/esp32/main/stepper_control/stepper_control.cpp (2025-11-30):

/*
 * stepper_control.cpp
 * Copyright (C) 2024 Havránek Kryštof <krystof@havrak.xyz>
 *
 * Distributed under terms of the MIT license.
 */

#include "stepper_control.h"
#define MAIN_TASK_SLEEP (200 / portTICK_PERIOD_MS)
StepperControl stepperControl = StepperControl();

StepperControl::StepperControl() { }

std::queue<gcode_command_t*> StepperControl::noProgrammQueue = std::queue<gcode_command_t*>();

void StepperControl::init()
{

	steppers.initMCPWN();
	steppers.initPCNT();
	steppers.initTimers();

	steppers.initStepperTasks();
	StepperControl::homingEventGroup = xEventGroupCreate();

	pinMode(CONFIG_STEPPER_Y_PIN_EN, OUTPUT);
	pinMode(CONFIG_STEPPER_P_PIN_EN, OUTPUT);
	ESP_LOGI(TAG, "commandSchedulerTask | stepper Y\n\tenable pin %d\n\tendstop pin %d\n\tstep pin %d\n\tsense pin %d\n\tdirection pin %d", CONFIG_STEPPER_Y_PIN_EN, CONFIG_STEPPER_Y_PIN_ENDSTOP, CONFIG_STEPPER_Y_PIN_STEP, CONFIG_STEPPER_Y_PIN_SENSE, CONFIG_STEPPER_Y_PIN_DIR);
	ESP_LOGI(TAG, "commandSchedulerTask | stepper P\n\tenable pin %d\n\tendstop pin %d\n\tstep pin %d\n\tsense pin %d\n\tdirection pin %d", CONFIG_STEPPER_P_PIN_EN, CONFIG_STEPPER_P_PIN_ENDSTOP, CONFIG_STEPPER_P_PIN_STEP, CONFIG_STEPPER_P_PIN_SENSE, CONFIG_STEPPER_P_PIN_DIR);
	gpio_set_level((gpio_num_t)CONFIG_STEPPER_Y_PIN_EN, 0);

	gpio_set_level((gpio_num_t)CONFIG_STEPPER_P_PIN_EN, 0);

	pinMode(CONFIG_STEPPER_Y_PIN_ENDSTOP, INPUT);
	pinMode(CONFIG_STEPPER_P_PIN_ENDSTOP, INPUT);

	noProgrammQueueLock = xSemaphoreCreateMutex();

	if (noProgrammQueueLock == NULL) {
		ESP_LOGE(TAG, "JoPkaEndpoint | xSemaphoreCreateMutex failed");
	} else {
		ESP_LOGI(TAG, "JoPkaEndpoint | created lock");
	}
	// on first step there are some initializations taking place that make it much longer than the rest
	steppers.stepStepper(stepperHalPitch, 1, 1, true);
	steppers.stepStepper(stepperHalYaw, 1, 1, true);

	xTaskCreate(StepperControl::commandSchedulerTask, "commandSchedulerTask", 4096, NULL, 5, &commandSchedulerTaskHandle);
}

float StepperControl::getElementFloat(const char* str, const uint16_t length, const uint16_t startIndex, const char* matchString, const uint16_t elementLength)
{
	bool negative = false;
	float toReturn = 0;
	uint8_t decimal = 0;
	for (uint16_t i = startIndex; i < length; i++) {
		if (str[i] == matchString[0]) {
			if (strncmp(str + i, matchString, elementLength) == 0) {

				// fix cases where matchString="P" will match "SP" and fail
				if (str[i - 1] >= 'A' && str[i - 1] <= 'Z')
					continue;

				i += elementLength;
				// fix cases where matchString="S" will match "SP" and fail
				if (!(str[i] == ' ' || str[i] == '-' || (str[i] >= '0' && str[i] <= '9')))
					continue;

				while (str[i] == ' ' && i < length)
					i++;

				if (str[i] == '-') {
					negative = true;
					i++;
				}
				while (str[i] != ' ' && i < length) {
					if (str[i] >= '0' && str[i] <= '9') {
						toReturn = toReturn * 10 + (str[i] - '0');
						if (decimal) {
							decimal++;
						}
						i++;
						continue;
					} else if (str[i] == '.' && !decimal) {
						decimal = 1;
						i++;
						continue;
					}
					return NAN;
				}
				toReturn /= pow(10, decimal);
				return negative ? -toReturn : toReturn;
			}
		}
	}
	return NAN;
}

int32_t StepperControl::getElementInt(const char* str, const uint16_t length, const uint16_t startIndex, const char* matchString, const uint16_t elementLength)
{
	bool negative = false;
	int32_t toReturn = 0;
	uint16_t iMatch = 0;
	for (uint16_t i = startIndex; i < length; i++) {
		if (str[i] == matchString[0]) {
			if (strncmp(str + i, matchString, elementLength) == 0) {

				// fix cases where matchString="P" will match "SP" and fail
				if (str[i - 1] >= 'A' && str[i - 1] <= 'Z')
					continue;

				i += elementLength;
				// fix cases where matchString="S" will match "SP" and fail
				if (!(str[i] == ' ' || str[i] == '-' || (str[i] >= '0' && str[i] <= '9')))
					continue;

				while (str[i] == ' ' && i < length)
					i++;

				if (str[i] == '-') {
					negative = true;
					i++;
				}
				while (str[i] != ' ' && i < length) {
					if (str[i] >= '0' && str[i] <= '9') {
						toReturn = toReturn * 10 + (str[i] - '0');
						i++;
						continue;
					}
					return GCODE_ELEMENT_INVALID_INT;
				}
				return negative ? -toReturn : toReturn;
			}
		}
	}
	return GCODE_ELEMENT_INVALID_INT;
}

bool StepperControl::getElementString(const char* str, const uint16_t length, const uint16_t startIndex, const char* matchString, const uint16_t elementLength)
{
	for (uint16_t i = startIndex; i < length; i++) {
		if (str[i] == matchString[0]) {
			if (strncmp(str + i, matchString, elementLength) == 0) {
				return true;
			}
		}
	}
	return false;
}
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

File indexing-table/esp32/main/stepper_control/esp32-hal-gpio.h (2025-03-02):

/*
	 Arduino.h - Main include file for the Arduino SDK
	 Copyright (c) 2005-2013 Arduino Team.  All right reserved.

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
	 You should have received a copy of the GNU Lesser General Public
	 License along with this library; if not, write to the Free Software
	 Foundation, Inc., 51 Franklin St, Fifth Floor, Boston, MA  02110-1301  USA
	 */

#ifndef MAIN_ESP32_HAL_GPIO_H_
#define MAIN_ESP32_HAL_GPIO_H_

#ifdef __cplusplus
extern "C" {
#endif

#include "esp_log.h"
#include "soc/adc_periph.h"
#include "soc/soc_caps.h"

#if CONFIG_IDF_TARGET_ESP32C6
#define NUM_OUPUT_PINS 46
#define PIN_DAC1 17
#define PIN_DAC2 18

#elif (CONFIG_IDF_TARGET_ESP32S2 || CONFIG_IDF_TARGET_ESP32S3)
#define NUM_OUPUT_PINS 46
#define PIN_DAC1 17
#define PIN_DAC2 18
#else
#define NUM_OUPUT_PINS 34
#define PIN_DAC1 25
#define PIN_DAC2 26
#endif

#define	LOW  0x0
#define	HIGH  0x1

	// GPIO FUNCTIONS
#define INPUT 0x01
#define OUTPUT 0x03
#define PULLUP 0x04
#define INPUT_PULLUP 0x05
#define PULLDOWN 0x08
#define INPUT_PULLDOWN 0x09
#define OPEN_DRAIN 0x10
#define OUTPUT_OPEN_DRAIN 0x12
#define ANALOG 0xC0
#define UNUSED 0xFF

	// Interrupt Modes

#define DISABLED 0x00
#define RISING 0x01
#define FALLING	0x02
#define CHANGE 0x03
#define ONLOW 0x04
#define ONHIGH 0x05
#define ONLOW_WE 0x0C
#define ONHIGH_WE 0x0D

#define digitalPinIsValid(pin) GPIO_IS_VALID_GPIO(pin)
#define digitalPinCanOutput(pin) GPIO_IS_VALID_OUTPUT_GPIO(pin)

#define digitalPinToRtcPin(pin) ((RTC_GPIO_IS_VALID_GPIO(pin)) ? rtc_io_number_get(pin) : -1)
#define digitalPinToDacChannel(pin) (((pin) == DAC_CHANNEL_1_GPIO_NUM) ? 0 : ((pin) == DAC_CHANNEL_2_GPIO_NUM) ? 1 : -1)

	void pinMode(uint8_t pin, uint8_t mode);
	void digitalWrite(uint8_t pin, uint8_t val);
	int digitalRead(uint8_t pin);

	void attachInterrupt(uint8_t pin, void (*)(void), uint8_t interruptType);
	void attachInterruptArg(uint8_t pin, void (*)(void*), void* arg, uint8_t interruptType);
	void detachInterrupt(uint8_t pin);

	int8_t digitalPinToTouchChannel(uint8_t pin);
	int8_t digitalPinToAnalogChannel(uint8_t pin);
	int8_t analogChannelToDigitalPin(uint8_t channel);

#ifdef __cplusplus
}
#endif

#endif /* MAIN_ESP32_HAL_GPIO_H_ */

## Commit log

2024-09-22 Added core component of esp32 firmware and updated some readmes
    [partitions.csv]
2024-09-22 Started work on serial interface of esp32
2024-09-29 Got DVR8833 stepper motor driver to work in 4 wire mode
2024-09-30 minor changes in esp32 firmware
2024-10-28 Minor changes in motor control, started extending gcode options
2024-10-29 Commit before rewrite to more efficient pwm creation
2024-10-30 Splitted codebase to testing version and full
    [partitions.csv]
2024-10-30 Forgot to stup PWM timer after we have triggered PCNT event
2024-10-30 Got PCNT + PWM combination to reliably work
2024-11-03 Ported tested stepper control method into main codebase
2024-11-03 Wrote stepper task, code not tested
2024-11-04 Done homing routine
2024-11-16 Only print of current position and handeling of G0 function remains
2024-11-16 Merged stepper Tasks to one, no clue if it will work well
2024-12-15 Added CST file for simulation of 24GHz antenna
2025-01-03 Added extension to ESP32 firmware to enable real time control
2025-01-28 Removed all references to tasker for ESP32 code
2025-02-05 StepperHal bug fixes
2025-02-17 ESP32: Cleanup of functions - mergedr horizontal and tilt functions into one
2025-02-17 ESP32: step relative and absolute function moved from anonymous
2025-02-22 ESP32: added loads of debug output to application layer
2025-02-24 ESP32: even more debug print
2025-02-24 ESP32: splitted parse Gcode function into five seperate ones
2025-02-24 ESP32: more bugfixes
2025-02-24 ESP32: few futher bug fixes
    [stepper_control.cpp, stepper_control.h]
2025-02-26 ESP32: fixes in parsing commands with arguments
    [stepper_control.cpp, stepper_control.h]
2025-02-26 ESP32: few more bugfixes
    [stepper_control.cpp, stepper_control.h]
2025-02-26 ESP32: few more bugfixes, still having trouble with pcnt when using program
    [stepper_control.cpp, stepper_control.h, stepper_hal.cpp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]
2025-03-01 ESP32: Found an obscure bug in stopNowStepper function that would lead to desynchronization
    [stepper_control.cpp, stepper_hal.cpp, stepper_hal.h]
2025-03-01 ESP32: removed useless os_core class, introduced helper timers into HAL to solve possible issue with syncrhonization
    [app_main.cpp, stepper_control.cpp, stepper_hal.cpp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]
2025-03-02 ESP32: timer was introduced to all stepper comamnds to maintain synchronization
2025-03-02 ESP32: extended homeming rotine to enabled homing axis independently
2025-03-02 ESP32: homing routine now works properly
2025-03-02 ESP32: move hal library to this project
2025-03-02 ESP32, MATLAB: debug log is displayed in MATLAB properly
2025-03-03 CAD: added cad files for all 3D printed components
    [SiDAR mount v14.f3d, horizontal endstop holder v5.f3d, rotary base 1 v7.f3d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]
2025-03-03 ESP32, MATLAB, DOC: Minor changes
2025-03-05 ESP32: fixes in position reporting
    [stepper_control.cpp, stepper_hal.cpp, stepper_hal.h]
2025-03-05 ESP32: more fixes in position reporting when using spindle
    [stepper_control.cpp, stepper_hal.cpp]
2025-03-17 ESP32: Added command to wait in application layer
2025-03-22 MATAB: changed naming scheme to yaw and pitch instead of everything else
2025-03-22 ESP32: changed naming scheme to yaw and pitch instead of everything else
2025-04-02 ESP32: Typo in spindle orientation
2025-04-02 MATLAB: fixed yaw indexing, now subcubes are correct size, rather ugly way it was done
2025-04-16 Switched to even more broken 122 GHz firmware
    [app_main.cpp, stepper_control.cpp]
2025-04-22 MATLAB: added slider to pick pitch angle in visualization
2025-04-29 ESP32: added M92 to change step count on the fly
2025-04-29 ESP32: moved M92 code to different part of the codebase
2025-04-29 MATLAB: added logic for yaw based cube clearing, changing stepcount, and more stuff related to preferences
2025-05-04 MATLAB: minor fixes in visualization
    [app_main.cpp]
2025-05-06 MATLAB: added symbolic documentation to all functions, added button to save screen to jpg
2025-05-07 ESP32, MATLAB, DOC: minor changes, got another flow chart to work in documentation
2025-05-08 DOC: added final flow diagram
2025-05-21 ESP32, MATLAB, DOC: minor fixes per recomendations
    [app_main.cpp, stepper_control.cpp, stepper_hal.cpp]
2025-05-21 CAD: added new model since last mount broke just now
    [SiDAR mount v16.f3d]
2025-05-22 ESP32: forgot brackets in stepper_hal leading to issues with absolute mode
    [stepper_control.cpp, stepper_hal.cpp]
2025-05-22 ESP32: minor fix
2025-08-13 stepper_hal: fixed bug in M82 command behaviour when in spindle regime
    [app_main.cpp, stepper_control.cpp, stepper_hal.cpp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]
2025-08-13 ESP32: stepper_hal.cpp, fixed small typo
    [stepper_hal.cpp]
2025-08-20 ESP32: stepper_control: unified homining method to be universal, added crude debounce
2025-08-20 CAD: added new version of yaw axis endstop mount
    [SiDAR mount v14.f3d, SiDAR mount.f3d, horizontal endstop holder v5.f3d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]
